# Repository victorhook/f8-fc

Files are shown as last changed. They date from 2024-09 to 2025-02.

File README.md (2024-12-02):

# f8 fc - Open source brushed x8 AIO

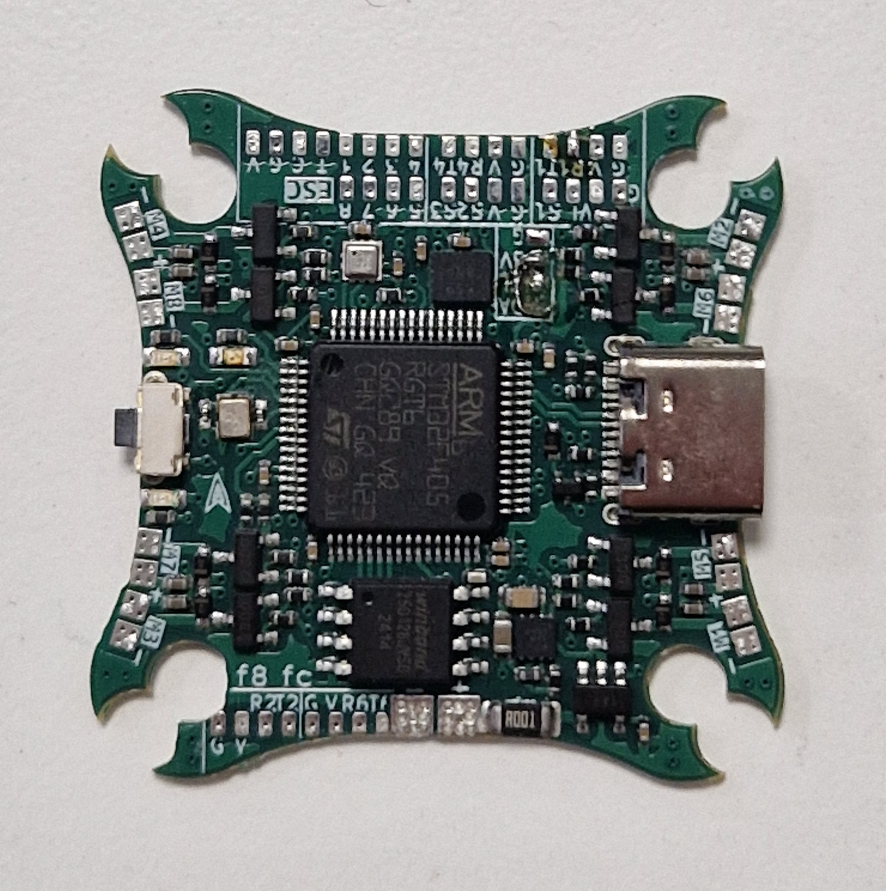
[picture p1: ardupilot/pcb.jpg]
PCB


[f8 fc](https://github.com/victorhook/f8-fc) is a fully open source AIO flight controller that is made primarily for small drones with brushed drones. It features:
- STM32F405 microcontroller with 1MB flash
- BMI270 imu
- BMP388 barometer
- Onboard 16MB external flash for data logging
- Status LEDs
- 1-4s input voltage
- 4 available UARTs
- **8** brushed motor drives with 6A mosfets
- Voltage & current sensing
- Runs ardupilot

## How to flash Ardupilot
1. Get ardupilot toolchain and put the `hwdef.dat` and `hwdef_bl.dat` in `ardupilot/libraries/AP_HAL_ChibiOS/hwdef/f8-fc/`
2. Build bootloader
```
./waf clean
./waf configure --board f8-fc --bootloader
./waf bootloader
```
3. Flash bootloader using something like STM32CubeProgrammer. Hold boot button when powering on the board to boot in DFU mode.
4. Build firmware and upload using the bootloader (have board plugged in to USB and ensure you get a new serial port)
```
./waf configure --board f8-fc
./waf copter --upload
```

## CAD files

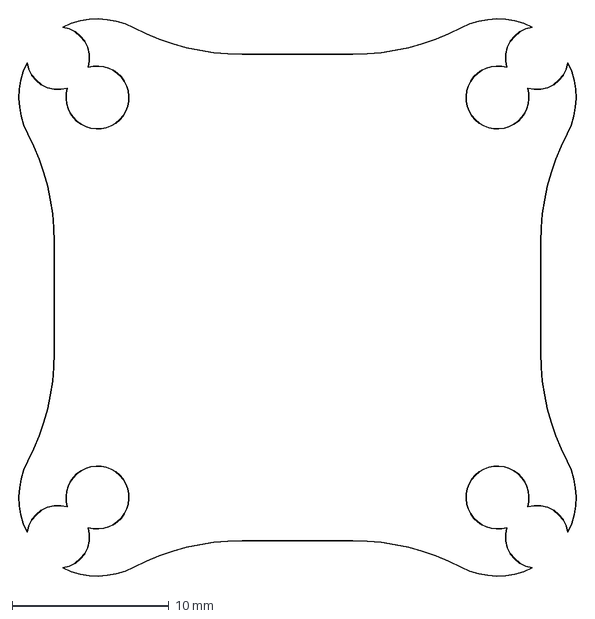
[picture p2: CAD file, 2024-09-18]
kicad/f8-fc-h7_rev-a/f8-fc_outline.dxf
35.9 x 35.9 mm

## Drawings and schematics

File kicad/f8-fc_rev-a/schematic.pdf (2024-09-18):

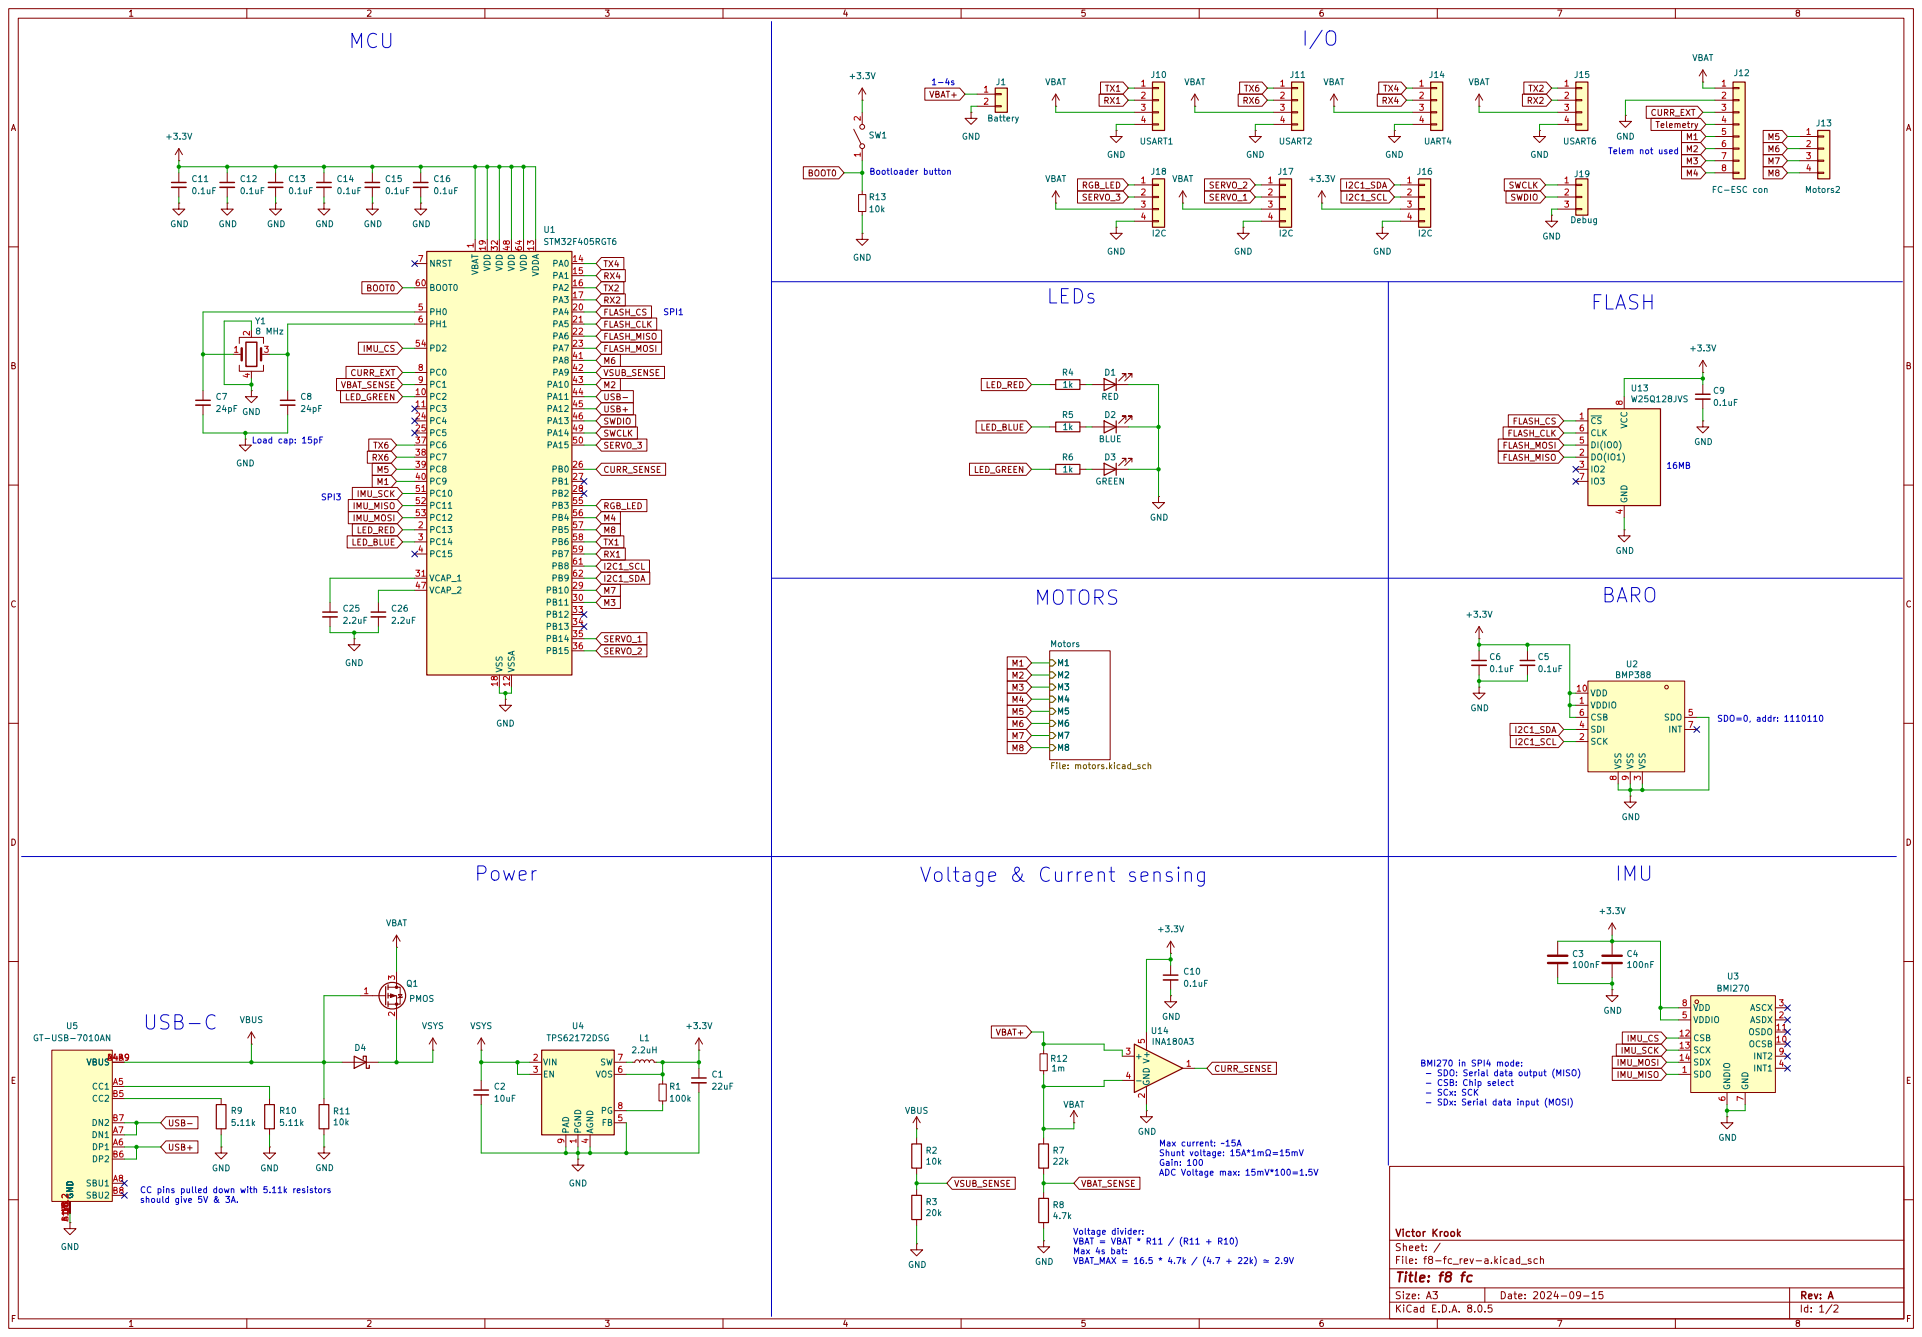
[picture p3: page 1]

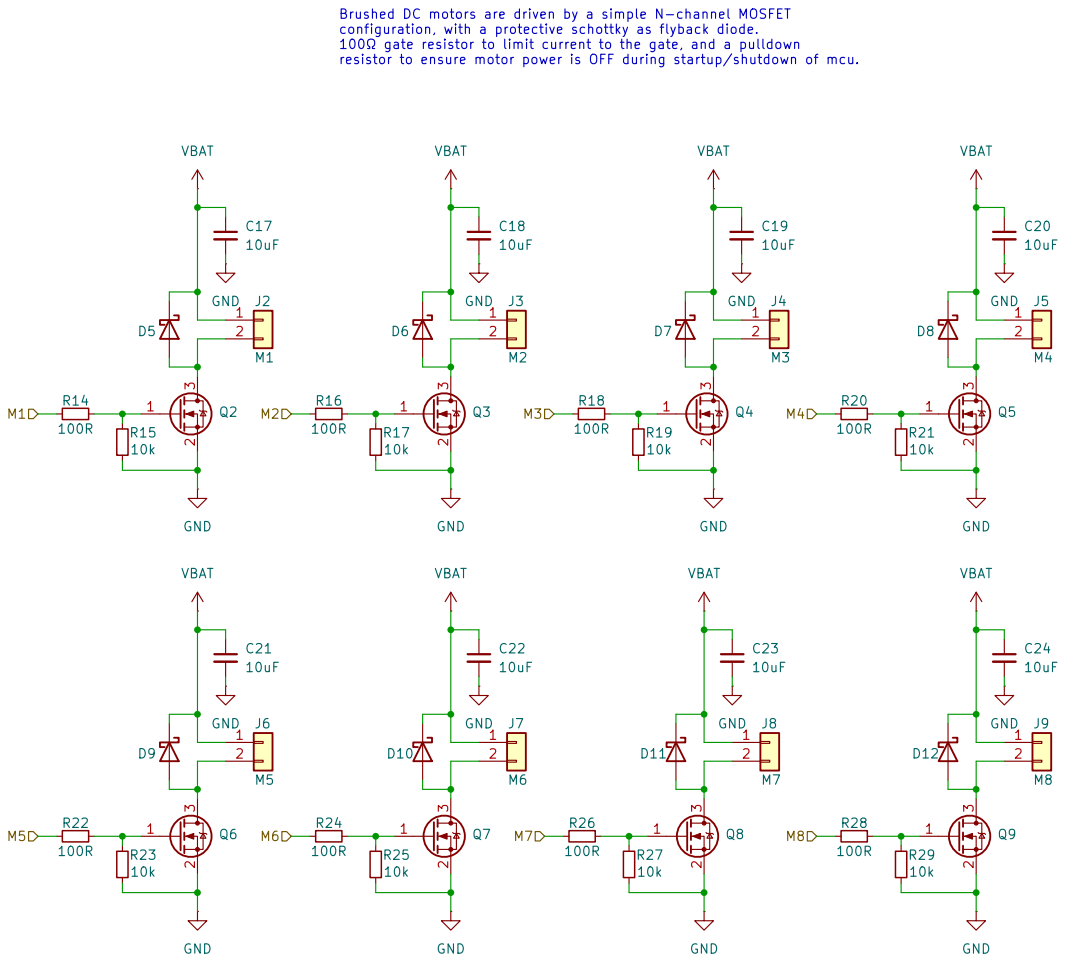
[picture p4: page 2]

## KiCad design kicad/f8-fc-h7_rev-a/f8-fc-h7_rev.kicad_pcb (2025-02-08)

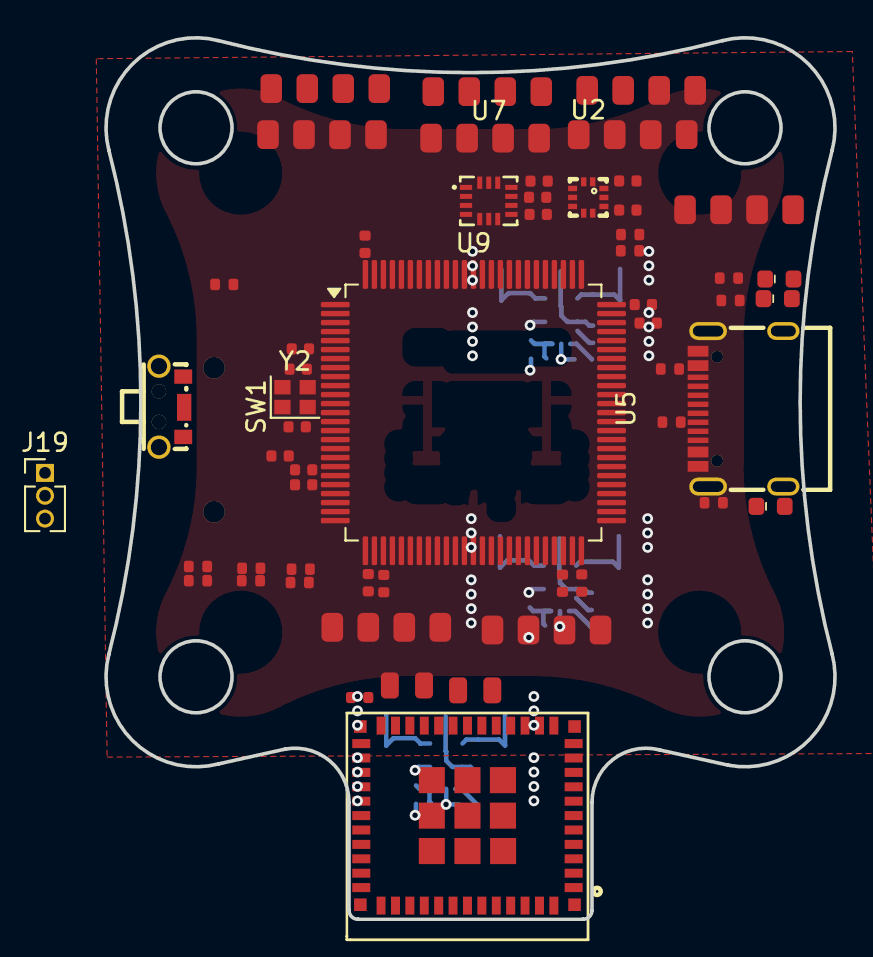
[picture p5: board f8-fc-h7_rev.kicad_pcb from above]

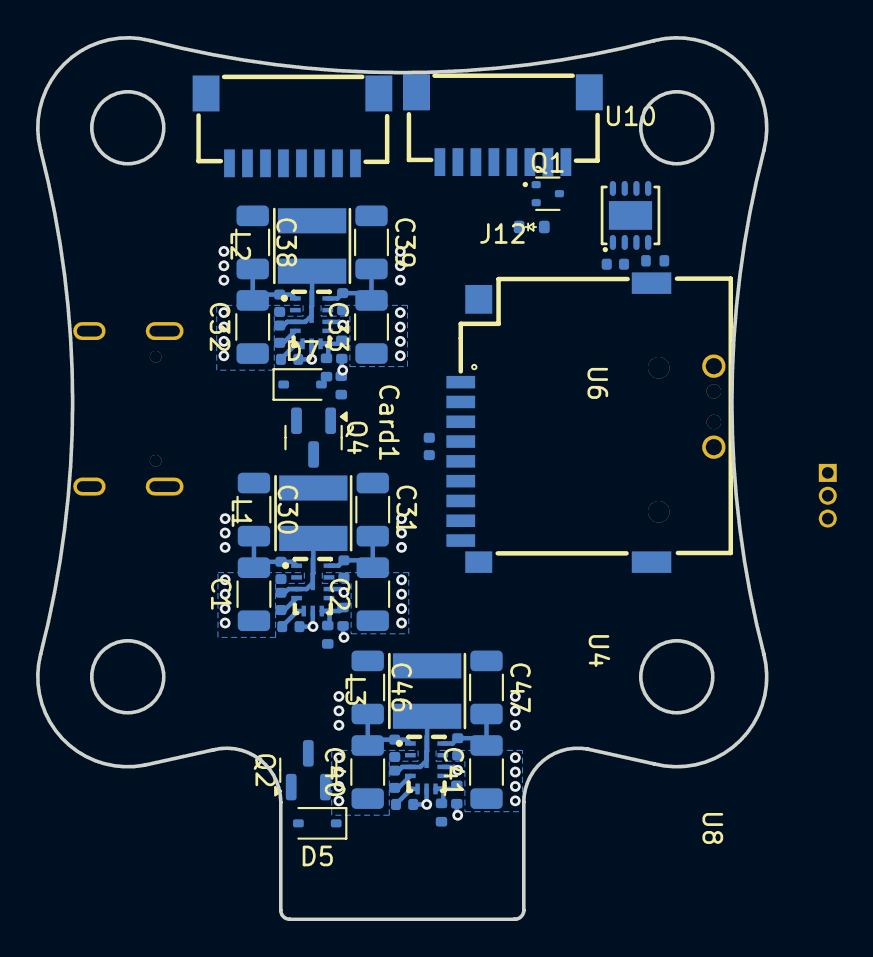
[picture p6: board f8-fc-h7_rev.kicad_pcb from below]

Board: 4 copper layers, 40.5 x 49.0 mm, 105 parts (50 on the bottom side), 46 nets.

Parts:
C1, C2, C32, C33, C40, C41: 10uF; C_1206_3216Metric
C3, C11: 10uF; C_0805_2012Metric_NoSilk
C4, C5, C6, C7, C9, C10, C17, C21, C22, C29, C37, C45, C48, C50, C52, C53, C54: 0.1uF; C_0402_1005Metric_NoSilk
C8: 4.7uF; C_0402_1005Metric_NoSilk
C18, C23: 15pF; C_0402_1005Metric_NoSilk
C19: 10nF; C_0402_1005Metric_NoSilk
C20, C49, C51: 2.2uF; C_0402_1005Metric_NoSilk
C24, C27, C34, C35, C42, C43: 220nF; C_0402_1005Metric_NoSilk
C28, C36, C44: 1uF; C_0402_1005Metric_NoSilk
C30, C31, C38, C39, C46, C47: 22uF; C_1206_3216Metric
Card1: TF PUSH; TF-SMD_TF-PUSH
D1: RED; LED_0603_1608Metric_NoSilk
D2: BLUE; LED_0603_1608Metric_NoSilk
D3: GREEN; LED_0603_1608Metric_NoSilk
D4: D_Schottky; D_SOD-523_NoSilk
D5, D7: D_Schottky; D_SOD-323
J1, J12: FC-ESC con; CONN-TH_SM08B-SRSS-TB-LF-SN
J10: USART1; Conn_4_Accesory_Bigger
J11: USART2; Conn_4_Accesory_Bigger
J14: UART4; Conn_4_Accesory_Bigger
J15: USART6; Conn_4_Accesory_Bigger
J16, J17, J18, J18#2, J18#3: I2C; Conn_4_Accesory_Bigger
J19: Debug; PinHeader_1x03_P1.27mm_Vertical
L1, L2, L3: 6.8uH; IND-SMD_L4.1-W4.1_ASFPIG4020
Q1: PMOS; SOT-523
Q2, Q4: WST4041; SOT-23
R1, R14, R16: 100k; R_0402_1005Metric_NoSilk
R2, R3, R11, R13, R20, R22, R23: 10k; R_0402_1005Metric_NoSilk
R4, R5, R6, R18: 1k; R_0402_1005Metric_NoSilk
R9, R10: 5.11k; R_0402_1005Metric_NoSilk
R12: 12.5K; R_0402_1005Metric_NoSilk
R15: 24.9k; R_0402_1005Metric_NoSilk
R17: 43.5k; R_0402_1005Metric_NoSilk
R24, R25: 2.2k; R_0402_1005Metric_NoSilk
R26: 120R; R_0402_1005Metric_NoSilk
SW1: SW_SPST; SW-SMD_TS-1086EV-16
U2: BMP388; SENSORM-SMD_BMP388
U3: ESP32-C3-MINI-1U-N4; WIFIM-SMD_61P-L13.2-W12.5-P0.80
U4, U6, U8: LMR33630AQRNXRQ1; VQFN-12_L3.0-W2.0-P0.65-BL_TI_RNX
U5: GT-USB-7010AN; USB-SMD_GT-USB-7010AN
U7: ICM-42688-P; LGA-14_L3.0-W2.5-P0.50-TL
U9: STM32H743VIT6; LQFP-100_14x14mm_P0.5mm
U10: SIT1050TK; TDFN-8_L3.0-W3.0-P0.65-BL-EP
Y2: 16 MHz; Crystal_SMD_2016-4Pin_2.0x1.6mm

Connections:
+3.3V: C3.1, C4.1, C5.1, C6.1, C8.1, C9.1, C10.1, C11.1, C17.1, C19.1, C20.1, C21.1, C22.1, C48.1, C50.1, C52.1, C53.1, C54.1, Card1.4 (VDD), J16.3, SW1.2 (B), U2.1 (VDDIO), U2.6 (CSB), U2.10 (VDD), U3.3 (3V3), U7.5 (VDDIO), U7.8 (VDD), U9.6 (VBAT), U9.11 (VDD), U9.20 (VREF+), U9.21 (VDDA), U9.27 (VDD), U9.50 (VDD), U9.75 (VDD), U9.100 (VDD), U10.5 (Vref)
+3V3: C46.1, C47.1, L3.2, R16.1, R24.1, R25.1
+4V5: C7.1, D7.1 (K), Q4.2 (S), U10.3 (VCC)
+5V: C30.1, C31.1, L1.2, Q4.3 (D), R1.1
+9V: C38.1, C39.1, L2.2, R14.1
BOOT0: R13.1, SW1.1 (A), U9.94 (BOOT0)
CANH: R26.1, U10.7 (CANH)
CANL: R26.2, U10.6 (CANL)
CURR_EXT: J1.3, J12.3
CURR_SENSE: R22.2, R23.1
GND: C1.2, C2.2, C3.2, C4.2, C5.2, C6.2, C7.2, C8.2, C9.2, C10.2, C11.2, C17.2, C18.2, C19.2, C20.2, C21.2, C22.2, C23.2, C24.2, C27.2, C28.1, C30.2, C31.2, C32.2, C33.2, C34.2, C35.2, C36.1, C38.2, C39.2, C40.2, C41.2, C42.2, C43.2, C44.1, C46.2, C47.2, C48.2, C49.2, C50.2, C51.2, C52.2, C53.2, C54.2, Card1.6 (VSS), D1.1 (K), D2.1 (K), D3.1 (K), J1.2, J10.4, J11.4, J12.2, J14.4, J15.4, J16.4, J17.4, J18.4, J18#2.4, J18#3.4, J19.3, R3.2, R9.2, R10.2, R12.2, R13.2, R15.2, R17.2, R18.2, R20.2, R23.2, U2.3 (VSS), U2.5 (SDO), U2.8 (VSS), U2.9 (VSS), U3.1 (GND), U3.2 (GND), U3.11 (GND), U3.14 (GND), U3.36 (GND), U3.37 (GND), U3.38 (GND), U3.39 (GND), U3.40 (GND), U3.41 (GND), U3.42 (GND), U3.43 (GND), U3.44 (GND), U3.45 (GND), U3.46 (GND), U3.47 (GND), U3.48 (GND), U3.49 (GND), U3.50 (GND), U3.51 (GND), U3.52 (GND), U3.53 (GND), U3.54 (GND), U3.55 (GND), U3.56 (GND), U3.57 (GND), U3.58 (GND), U3.59 (GND), U3.60 (GND), U3.61 (GND), U4.1 (PGND), U4.6 (AGND), U4.11 (PGND), U5.13 (GND), U5.14 (GND), U5.15 (GND), U5.16 (GND), U5.A1B12 (GND), U5.B1A12 (GND), U6.1 (PGND), U6.6 (AGND), U6.11 (PGND), U7.6 (GND), U8.1 (PGND), U8.6 (AGND), U8.11 (PGND), U9.10 (VSS), U9.19 (VSSA), U9.26 (VSS), U9.49 (VSS), U9.74 (VSS), U9.99 (VSS), U10.2 (GND), U10.8 (S), U10.9 (EP), Y2.2, Y2.4
I2C1_SCL: J16.2, R25.2, U2.2 (SCK)
I2C1_SDA: J16.1, R24.2, U2.4 (SDI)
unnamed: C49.1, U9.48 (VCAP)
unnamed: C51.1, U9.73 (VCAP)
unnamed: D1.2 (A), R4.1
unnamed: D2.2 (A), R5.1
unnamed: D3.2 (A), R6.1
unnamed: C29.1, U4.4 (BOOT)
unnamed: R1.2, R12.1, U4.7 (FB)
unnamed: C29.2, L1.1, U4.3 (NC), U4.12 (SW)
unnamed: C28.2, U4.5 (VCC)
unnamed: R10.1, U5.A5 (CC1)
unnamed: R9.1, U5.B5 (CC2)
unnamed: C37.1, U6.4 (BOOT)
unnamed: R14.2, R15.1, U6.7 (FB)
unnamed: C37.2, L2.1, U6.3 (NC), U6.12 (SW)
unnamed: C36.2, U6.5 (VCC)
unnamed: C45.1, U8.4 (BOOT)
unnamed: R16.2, R17.1, U8.7 (FB)
unnamed: C45.2, L3.1, U8.3 (NC), U8.12 (SW)
unnamed: C44.2, U8.5 (VCC)
unnamed: C18.1, U9.12 (PH0), Y2.1
unnamed: C23.1, U9.13 (PH1), Y2.3
RGB_LED: J18.1, J18#2.1, J18#3.1
SERVO_3: J18.2, J18#2.2, J18#3.2
SWCLK: J19.1, U9.76 (PA14)
SWDIO: J19.2, U9.72 (PA13)
Telemetry: J1.4, J12.4
USB+: U5.A6 (DP1), U5.B6 (DP2), U9.71 (PA12)
USB-: U5.A7 (DN1), U5.B7 (DN2), U9.70 (PA11)
VBAT: C1.1, C2.1, C24.1, C27.1, C32.1, C33.1, C34.1, C35.1, J1.1, J10.3, J11.3, J12.1, J14.3, J15.3, J17.3, J18.3, J18#2.3, J18#3.3, Q1.3 (D), R11.1, U4.2 (VIN), U4.9 (EN), U4.10 (VIN), U6.2 (VIN), U6.9 (EN), U6.10 (VIN)
VBAT_SENSE: R11.2, R18.1
VBUS: D4.2 (A), D5.2 (A), D7.2 (A), Q1.1 (G), Q4.1 (G), R2.1, R20.1, U5.A4B9 (VBUS), U5.B4A9 (VBUS)
VSUB_SENSE: R2.2, R3.1, U9.68 (PA9)
VSYS: C40.1, C41.1, C42.1, C43.1, D4.1 (K), D5.1 (K), Q1.2 (S), U8.2 (VIN), U8.9 (EN), U8.10 (VIN)

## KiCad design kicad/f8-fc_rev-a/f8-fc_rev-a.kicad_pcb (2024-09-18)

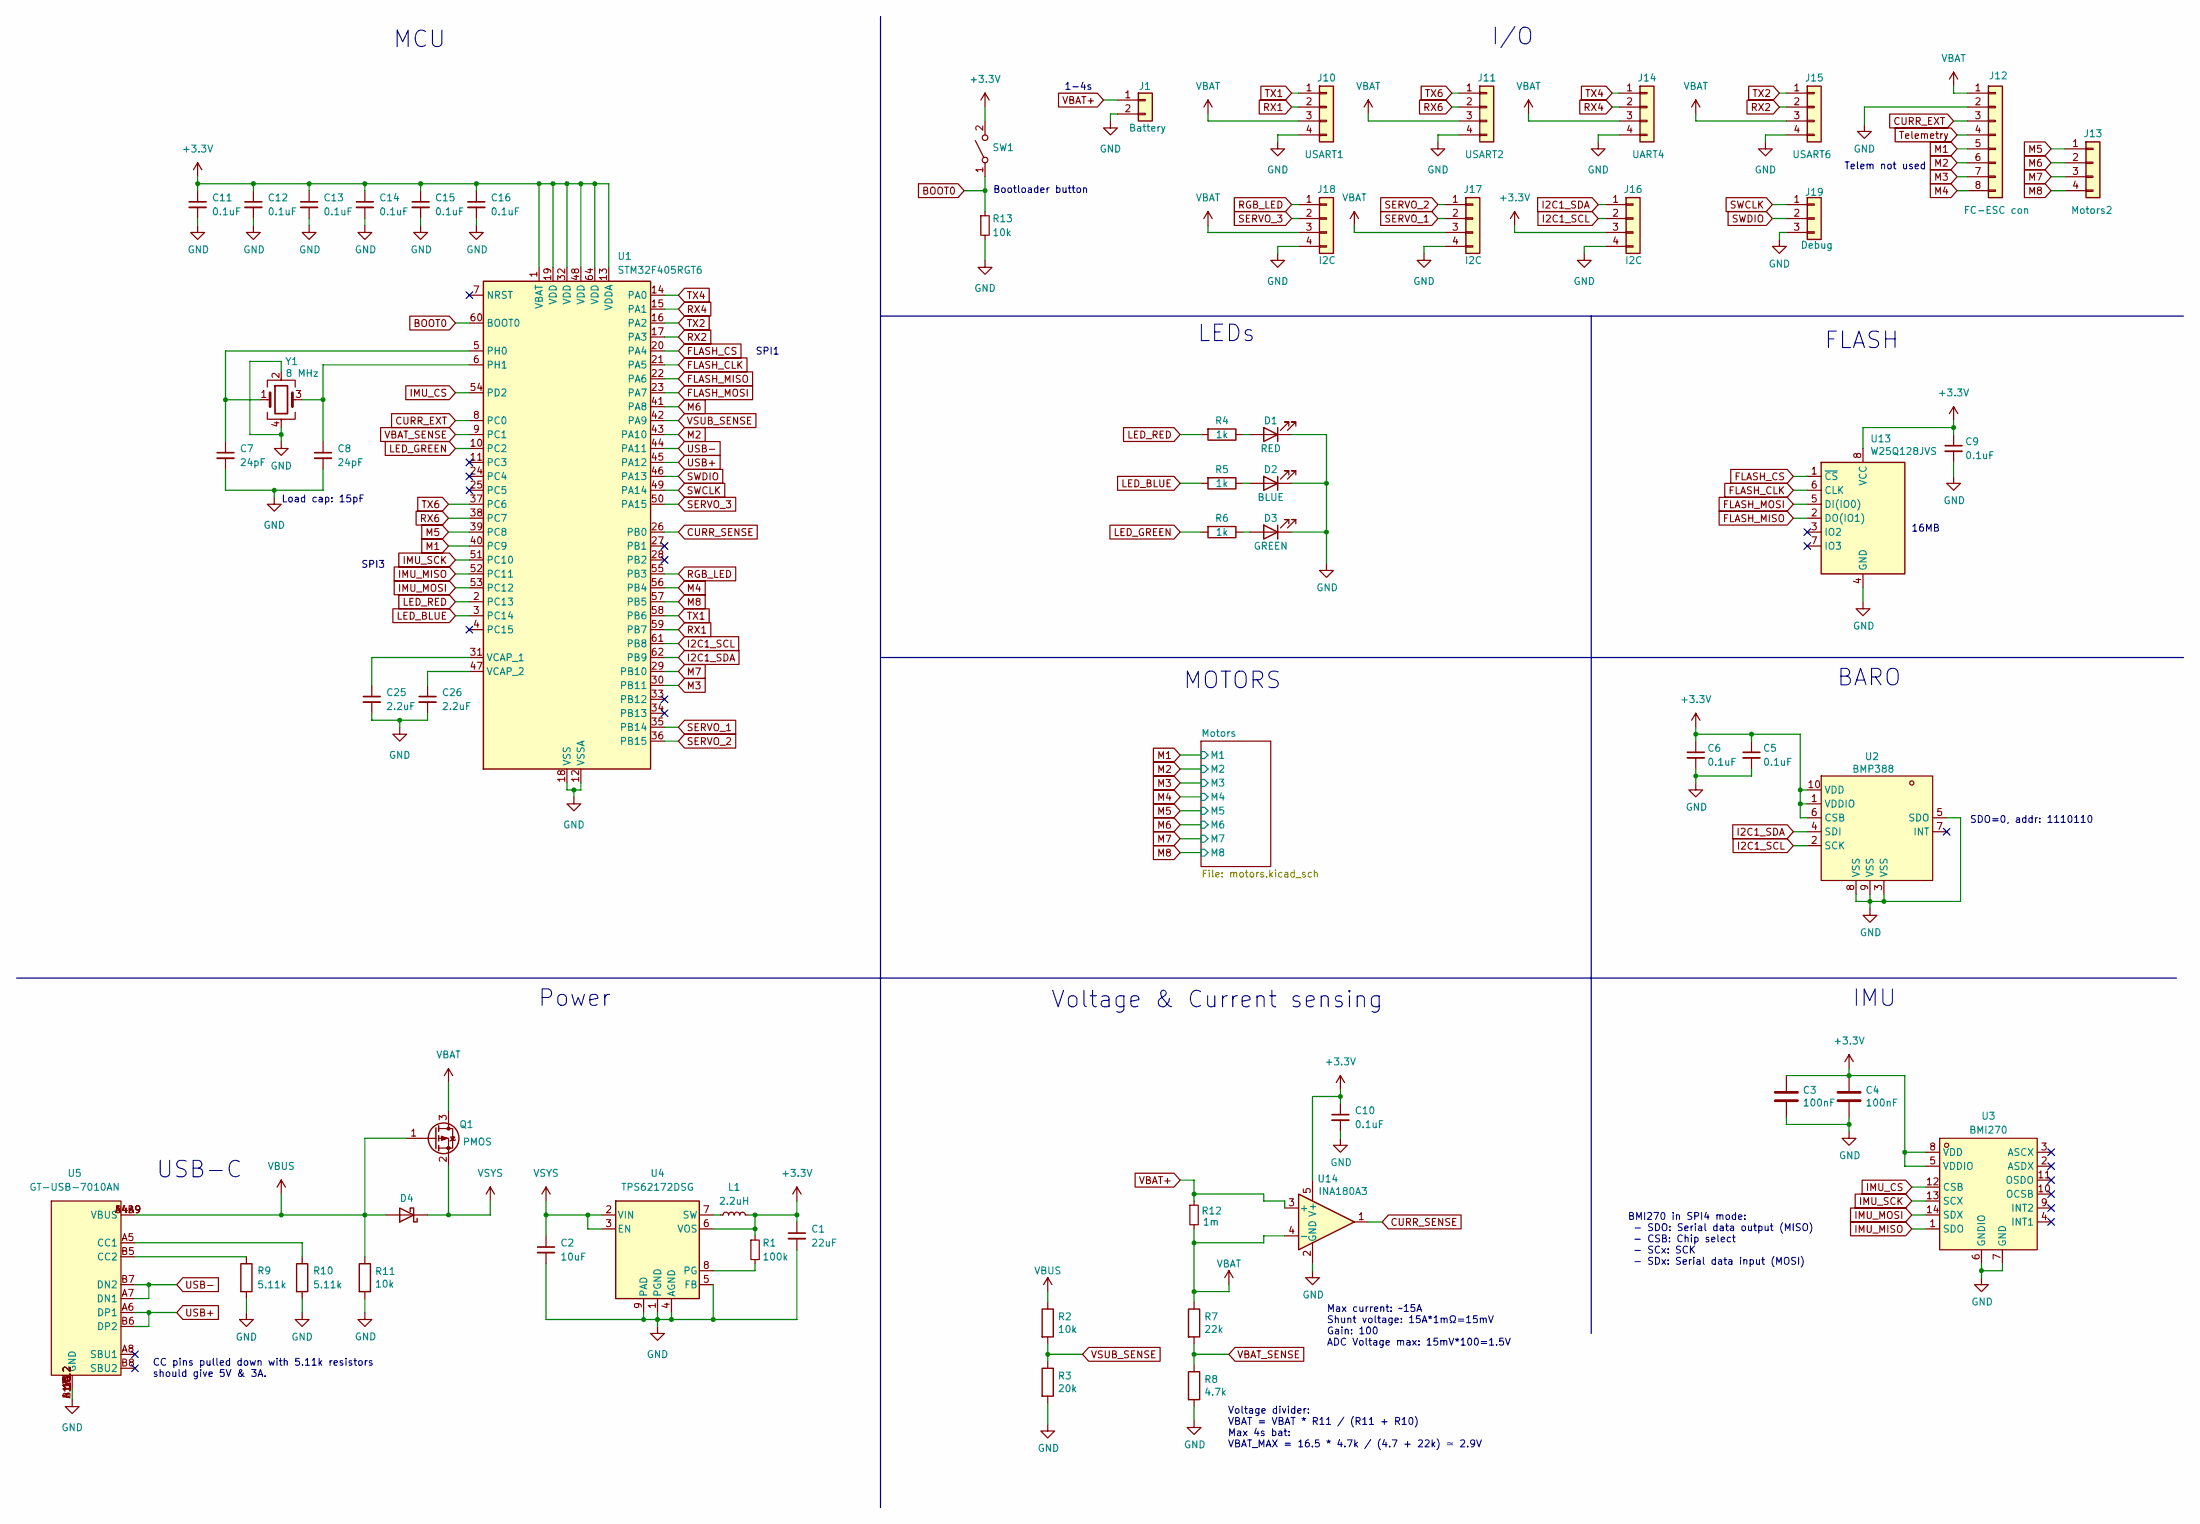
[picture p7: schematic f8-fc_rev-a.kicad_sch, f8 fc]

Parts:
C1: 22uF; C_0603_1608Metric_NoSilk
C2: 10uF; C_0603_1608Metric_NoSilk
C3, C4: 100nF; C_0402_1005Metric_NoSilk
C5, C6, C9, C10, C11, C12, C13, C14, C15, C16: 0.1uF; C_0402_1005Metric_NoSilk
C7, C8: 24pF; C_0402_1005Metric_NoSilk
C25, C26: 2.2uF; C_0402_1005Metric_NoSilk
D1: RED; LED_0603_1608Metric_NoSilk
D2: BLUE; LED_0603_1608Metric_NoSilk
D3: GREEN; LED_0603_1608Metric_NoSilk
D4: D_Schottky; D_SOD-523_NoSilk; LCSC Part C455040
J1: Battery; Conn_2_Bat
J10: USART1; Conn_4_Accesory
J11: USART2; Conn_4_Accesory
J12: FC-ESC con; Conn_8_Accesory
J13: Motors2; Conn_4_Accesory
J14: UART4; Conn_4_Accesory
J15: USART6; Conn_4_Accesory
J16, J17, J18: I2C; Conn_4_Accesory
J19: Debug; PinHeader_1x03_P1.27mm_Vertical
L1: 2.2uH; L_0402_1005Metric
Q1: PMOS; SOT-523; LCSC Part C5334586
R1: 100k; R_0402_1005Metric_NoSilk
R2, R11, R13: 10k; R_0402_1005Metric_NoSilk
R3: 20k; R_0402_1005Metric_NoSilk
R4, R5, R6: 1k; R_0402_1005Metric_NoSilk
R7: 22k; R_0402_1005Metric_NoSilk
R8: 4.7k; R_0402_1005Metric_NoSilk
R9, R10: 5.11k; R_0402_1005Metric_NoSilk
R12: 1m; R_1206_3216Metric; LCSC Part C7419993
SW1: SW_SPST; SW-SMD_TS-1086EV-16
U1: STM32F405RGT6; LQFP-64_10x10mm_P0.5mm
U2: BMP388; SENSORM-SMD_BMP388; LCSC Part C779278
U3: BMI270; LGA-14_L3.0-W2.5-P0.50-BR; LCSC Part C2836813
U4: TPS62172DSG; WSON-8-1EP_2x2mm_P0.5mm_EP0.9x1.6mm_ThermalVias
U5: GT-USB-7010AN; USB-SMD_GT-USB-7010AN; LCSC Part C963370
U13: W25Q128JVS; SOIC-8_5.23x5.23mm_P1.27mm; LCSC Part C97521
U14: INA180A3; SOT-23-5; LCSC Part C122882
Y1: 8 MHz; Crystal_SMD_2016-4Pin_2.0x1.6mm; LCSC Part C2831375

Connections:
+3.3V: C1.1, C3.1, C4.1, C5.1, C6.1, C9.1, C10.1, C11.1, C12.1, C13.1, C14.1, C15.1, C16.1, J16.3, L1.2, R1.1, SW1.2 (B), U1.1 (VBAT), U1.13 (VDDA), U1.19 (VDD), U1.32 (VDD), U1.48 (VDD), U1.64 (VDD), U2.1 (VDDIO), U2.6 (CSB), U2.10 (VDD), U3.5 (VDDIO), U3.8 (VDD), U4.6 (VOS), U13.8 (VCC), U14.5 (V+)
BOOT0: R13.1, SW1.1 (A), U1.60 (BOOT0)
CURR_EXT: J12.3, U1.8 (PC0)
CURR_SENSE: U1.26 (PB0), U14.1
FLASH_CLK: U1.21 (PA5), U13.6 (CLK)
FLASH_CS: U1.20 (PA4), U13.1 (~CS)
FLASH_MISO: U1.22 (PA6), U13.2 (DO(IO1))
FLASH_MOSI: U1.23 (PA7), U13.5 (DI(IO0))
GND: C1.2, C2.2, C3.2, C4.2, C5.2, C6.2, C7.2, C8.2, C9.2, C10.2, C11.2, C12.2, C13.2, C14.2, C15.2, C16.2, C25.2, C26.2, D1.1 (K), D2.1 (K), D3.1 (K), J1.2, J10.4, J11.4, J12.2, J14.4, J15.4, J16.4, J17.4, J18.4, J19.3, R3.2, R8.2, R9.2, R10.2, R11.2, R13.2, U1.12 (VSSA), U1.18 (VSS), U1.63 (VSS), U2.3 (VSS), U2.5 (SDO), U2.8 (VSS), U2.9 (VSS), U3.6 (GNDIO), U3.7 (GND), U4.1 (PGND), U4.4 (AGND), U4.5 (FB), U4.9 (PAD), U5.13 (GND), U5.14 (GND), U5.15 (GND), U5.16 (GND), U5.A1B12 (GND), U5.B1A12 (GND), U13.4 (GND), U14.2 (GND), Y1.2, Y1.4; also elsewhere on the board
I2C1_SCL: J16.2, U1.61 (PB8), U2.2 (SCK)
I2C1_SDA: J16.1, U1.62 (PB9), U2.4 (SDI)
IMU_CS: U1.54 (PD2), U3.12 (CSB)
IMU_MISO: U1.52 (PC11), U3.1 (SDO)
IMU_MOSI: U1.53 (PC12), U3.14 (SDX)
IMU_SCK: U1.51 (PC10), U3.13 (SCX)
LED_BLUE: R5.2, U1.3 (PC14)
LED_GREEN: R6.2, U1.10 (PC2)
LED_RED: R4.2, U1.2 (PC13)
M1: J12.5, U1.40 (PC9); also elsewhere on the board
M2: J12.6, U1.43 (PA10); also elsewhere on the board
M3: J12.7, U1.30 (PB11); also elsewhere on the board
M4: J12.8, U1.56 (PB4); also elsewhere on the board
M5: J13.1, U1.39 (PC8); also elsewhere on the board
M6: J13.2, U1.41 (PA8); also elsewhere on the board
M7: J13.3, U1.29 (PB10); also elsewhere on the board
M8: J13.4, U1.57 (PB5); also elsewhere on the board
unnamed: D1.2 (A), R4.1
unnamed: D2.2 (A), R5.1
unnamed: D3.2 (A), R6.1
unnamed: C7.1, U1.5 (PH0), Y1.1
unnamed: C8.1, U1.6 (PH1), Y1.3
unnamed: C25.1, U1.31 (VCAP_1)
unnamed: C26.1, U1.47 (VCAP_2)
unnamed: R1.2, U4.8 (PG)
unnamed: L1.1, U4.7 (SW)
unnamed: R10.1, U5.A5 (CC1)
unnamed: R9.1, U5.B5 (CC2)
RGB_LED: J18.1, U1.55 (PB3)
RX1: J10.2, U1.59 (PB7)
RX2: J15.2, U1.17 (PA3)
RX4: J14.2, U1.15 (PA1)
RX6: J11.2, U1.38 (PC7)
SERVO_1: J17.2, U1.35 (PB14)
SERVO_2: J17.1, U1.36 (PB15)
SERVO_3: J18.2, U1.50 (PA15)
SWCLK: J19.1, U1.49 (PA14)
SWDIO: J19.2, U1.46 (PA13)
TX1: J10.1, U1.58 (PB6)
TX2: J15.1, U1.16 (PA2)
TX4: J14.1, U1.14 (PA0)
TX6: J11.1, U1.37 (PC6)
Telemetry: J12.4
USB+: U1.45 (PA12), U5.A6 (DP1), U5.B6 (DP2)
USB-: U1.44 (PA11), U5.A7 (DN1), U5.B7 (DN2)
VBAT: J10.3, J11.3, J12.1, J14.3, J15.3, J17.3, J18.3, Q1.3 (D), R7.1, R12.2, U14.4 (-); also elsewhere on the board
VBAT+: J1.1, R12.1, U14.3 (+)
VBAT_SENSE: R7.2, R8.1, U1.9 (PC1)
VBUS: D4.2 (A), Q1.1 (G), R2.1, R11.1, U5.A4B9 (VBUS), U5.B4A9 (VBUS)
VSUB_SENSE: R2.2, R3.1, U1.42 (PA9)
VSYS: C2.1, D4.1 (K), Q1.2 (S), U4.2 (VIN), U4.3 (EN)

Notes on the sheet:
Max current: ~15A Shunt voltage: 15A*1mΩ=15mV Gain: 100 ADC Voltage max: 15mV*100=1.5V
MCU
SDO=0, addr: 1110110
BMI270 in SPI4 mode: - SDO: Serial data output (MISO) - CSB: Chip select - SCx: SCK - SDx: Serial data input (MOSI)
16MB
Telem not used
Voltage & Current sensing
LEDs
FLASH
IMU
I/O
CC pins pulled down with 5.11k resistors should give 5V & 3A.
Bootloader button
BARO
Load cap: 15pF
Voltage divider: VBAT = VBAT * R11 / (R11 + R10) Max 4s bat: VBAT_MAX = 16.5 * 4.7k / (4.7 + 22k) ≃ 2.9V
Power
SPI3
USB-C
SPI1
1-4s
MOTORS

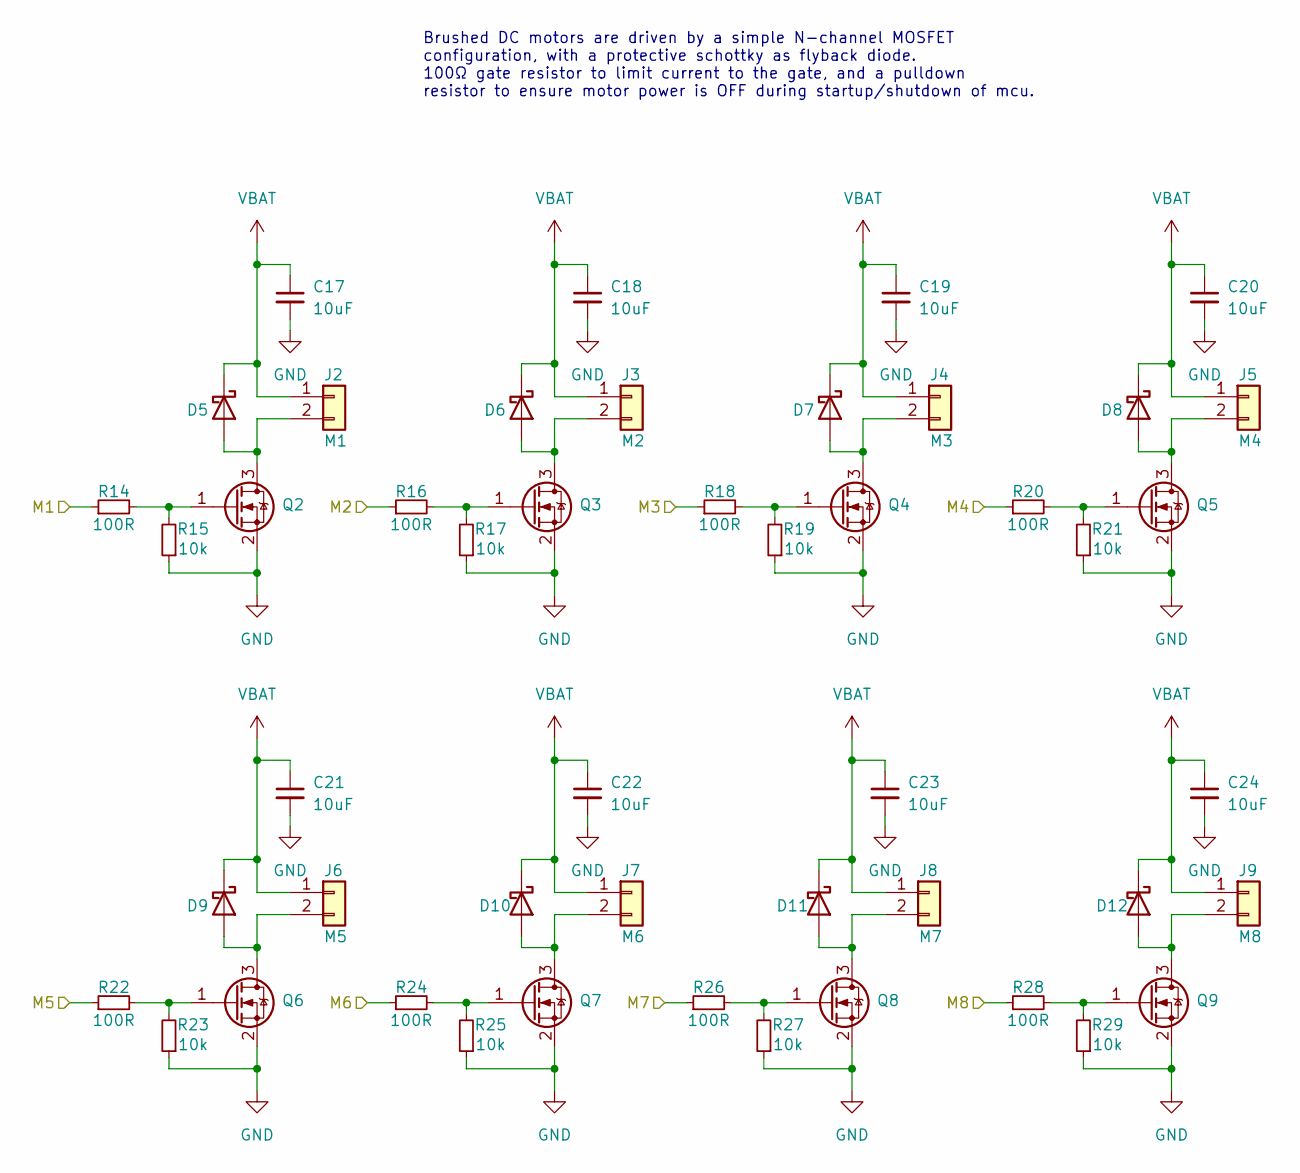
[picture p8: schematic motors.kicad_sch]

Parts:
C17, C18, C19, C20, C21, C22, C23, C24: 10uF; C_0402_1005Metric_NoSilk
D5, D6, D7, D8, D9, D10, D11, D12: D_Schottky; D_SOD-523_NoSilk; LCSC Part C455040
J2: M1; Conn_2_Motors
J3: M2; Conn_2_Motors
J4: M3; Conn_2_Motors
J5: M4; Conn_2_Motors
J6: M5; Conn_2_Motors
J7: M6; Conn_2_Motors
J8: M7; Conn_2_Motors
J9: M8; Conn_2_Motors
Q2, Q3, Q4, Q5, Q6, Q7, Q8, Q9: 2300A; SOT-23_NoSilk; LCSC Part C7437077
R14, R16, R18, R20, R22, R24, R26, R28: 100R; R_0402_1005Metric_NoSilk
R15, R17, R19, R21, R23, R25, R27, R29: 10k; R_0402_1005Metric_NoSilk

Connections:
GND: C17.2, C18.2, C19.2, C20.2, C21.2, C22.2, C23.2, C24.2, Q2.2 (S), Q3.2 (S), Q4.2 (S), Q5.2 (S), Q6.2 (S), Q7.2 (S), Q8.2 (S), Q9.2 (S), R15.1, R17.1, R19.1, R21.1, R23.1, R25.1, R27.1, R29.1; also elsewhere on the board
M1: R14.1; also elsewhere on the board
M2: R16.1; also elsewhere on the board
M3: R18.1; also elsewhere on the board
M4: R20.1; also elsewhere on the board
M5: R22.1; also elsewhere on the board
M6: R24.1; also elsewhere on the board
M7: R26.1; also elsewhere on the board
M8: R28.1; also elsewhere on the board
unnamed: D5.2 (A), J2.2, Q2.3 (D)
unnamed: D6.2 (A), J3.2, Q3.3 (D)
unnamed: D7.2 (A), J4.2, Q4.3 (D)
unnamed: D8.2 (A), J5.2, Q5.3 (D)
unnamed: D9.2 (A), J6.2, Q6.3 (D)
unnamed: D10.2 (A), J7.2, Q7.3 (D)
unnamed: D11.2 (A), J8.2, Q8.3 (D)
unnamed: D12.2 (A), J9.2, Q9.3 (D)
unnamed: Q2.1 (G), R14.2, R15.2
unnamed: Q3.1 (G), R16.2, R17.2
unnamed: Q4.1 (G), R18.2, R19.2
unnamed: Q5.1 (G), R20.2, R21.2
unnamed: Q6.1 (G), R22.2, R23.2
unnamed: Q7.1 (G), R24.2, R25.2
unnamed: Q8.1 (G), R26.2, R27.2
unnamed: Q9.1 (G), R28.2, R29.2
VBAT: C17.1, C18.1, C19.1, C20.1, C21.1, C22.1, C23.1, C24.1, D5.1 (K), D6.1 (K), D7.1 (K), D8.1 (K), D9.1 (K), D10.1 (K), D11.1 (K), D12.1 (K), J2.1, J3.1, J4.1, J5.1, J6.1, J7.1, J8.1, J9.1; also elsewhere on the board

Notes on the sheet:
Brushed DC motors are driven by a simple N-channel MOSFET configuration, with a protective schottky as flyback diode. 100Ω gate resistor to limit current to the gate, and a pulldown resistor to ensure motor power is OFF during startup/shutdown of mcu.

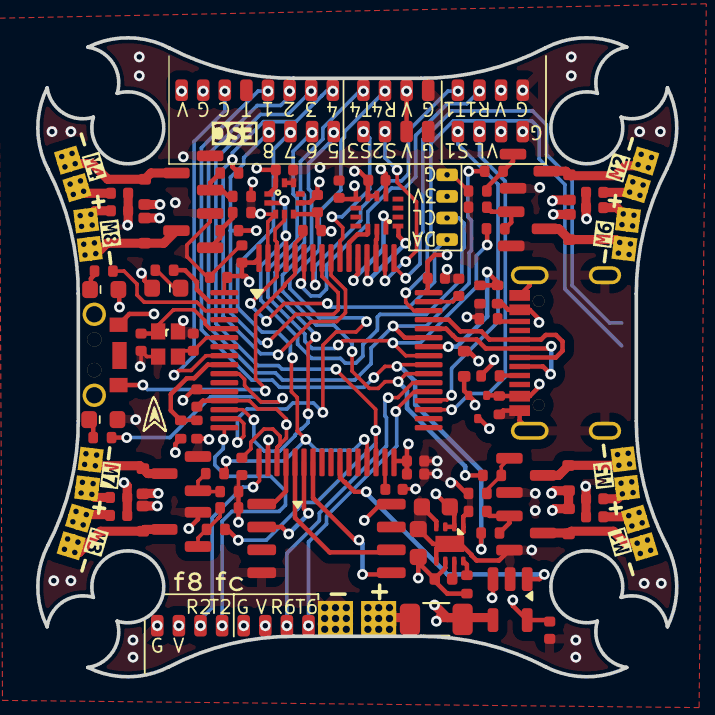
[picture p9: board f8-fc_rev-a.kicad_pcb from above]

Board: 4 copper layers, 35.5 x 35.5 mm, 114 parts (1 on the bottom side), 75 nets.

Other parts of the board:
kibuzzard-66DD79C8: G***; kibuzzard-66DD79C8
kibuzzard-66DD79DA: G***; kibuzzard-66DD79DA
kibuzzard-66DD778E: G***; kibuzzard-66DD778E
kibuzzard-66DD7786: G***; kibuzzard-66DD7786
kibuzzard-66E556E1: G***; kibuzzard-66E556E1
kibuzzard-66E556E7: G***; kibuzzard-66E556E7
kibuzzard-66E3374B: G***; kibuzzard-66E3374B
kibuzzard-66E5570F: G***; kibuzzard-66E5570F
kibuzzard-66E55715: G***; kibuzzard-66E55715

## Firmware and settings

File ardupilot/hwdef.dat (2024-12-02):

# hw definition file for processing by chibios_hwdef.py
# for f8 fc hardware.

# MCU class and specific type
# STM32F405RGT6
MCU STM32F4xx STM32F405xx

# board ID for firmware load
APJ_BOARD_ID 1299

# crystal frequency, setup to use external oscillator
OSCILLATOR_HZ 16000000

FLASH_SIZE_KB 1024

# bootloader takes first sector
FLASH_RESERVE_START_KB 64

define HAL_STORAGE_SIZE 16384
define STORAGE_FLASH_PAGE 1

STM32_ST_USE_TIMER 5

#optimize for space
env OPTIMIZE -Os

# These are the pins for SWD debugging with a STlinkv2 or black-magic probe.
PA13 JTMS-SWDIO SWD
PA14 JTCK-SWCLK SWD

# -- USB -- #
USB_STRING_MANUFACTURER "f8 fc"

# USB
PA11 OTG_FS_DM OTG1
PA12 OTG_FS_DP OTG1

# OTG USB VBUS (USB detect)
#PA9 VBUS INPUT

# -- SPI devices -- ##
SPIDEV bmi270    SPI3 DEVID1 IMU_CS    MODE3 10*MHZ 10*MHZ
SPIDEV dataflash SPI1 DEVID2 FLASH_CS  MODE3 32*MHZ 32*MHZ

# SPI1 for W25Q128JVS dataflash
PA5 SPI1_SCK SPI1
PA6 SPI1_MISO SPI1
PA7 SPI1_MOSI SPI1
PA4 FLASH_CS CS

# SPI3 for BMI270 IMU
PC10 SPI3_SCK SPI3
PC11 SPI3_MISO SPI3
PC12 SPI3_MOSI SPI3
PD2 IMU_CS CS

# -- SERIAL ports -- #
SERIAL_ORDER OTG1 USART1 USART2 UART4 USART6

# USART1
PB6 USART1_TX USART1
PB7 USART1_RX USART1

# USART2
PA2 USART2_TX USART2
PA3 USART2_RX USART2

# UART4
PA0 UART4_TX UART4 NODMA
PA1 UART4_RX UART4 NODMA

# USART6
PC6 USART6_TX USART6
PC7 USART6_RX USART6

# -- I2C ports -- #
I2C_ORDER I2C1

# I2C1
PB8 I2C1_SCL I2C1
PB9 I2C1_SDA I2C1

# -- ADC ports -- #
define HAL_BATT_MONITOR_DEFAULT 4

# Current
PB0 BATT_CURRENT_SENS ADC1 SCALE(1)
define HAL_BATT_CURR_PIN 8
define HAL_BATT_CURR_SCALE 70.8

# Voltage
PC1 BATT_VOLTAGE_SENS ADC1 SCALE(1)
define HAL_BATT_VOLT_PIN 11
define HAL_BATT_VOLT_SCALE 11.0

# Current (external)
PC0 BATT_CURRENT_SENS2 ADC1 SCALE(1)
define HAL_BATT2_CURR_PIN 10
define HAL_BATT2_CURR_SCALE 10

# Voltage (external, same pin as internal)
define HAL_BATT2_VOLT_PIN 11
define HAL_BATT2_VOLT_SCALE 11.0

# -- MOTORS -- #
PC9  TIM3_CH4  TIM3  PWM(1) GPIO(50) # M1
PA10 TIM1_CH3  TIM1  PWM(2) GPIO(51) # M2
PB11 TIM2_CH4  TIM2  PWM(3) GPIO(52) # M3
PB4  TIM3_CH1  TIM3  PWM(4) GPIO(53) # M4
PC8  TIM3_CH3  TIM3  PWM(5) GPIO(54) # M5
PA8  TIM1_CH1  TIM1  PWM(6) GPIO(55) # M6
PB10 TIM2_CH3  TIM2  PWM(7) GPIO(56) # M7
PB5  TIM3_CH2  TIM3  PWM(8) GPIO(57) # M8

# -- Servos -- #
PB15 TIM12_CH2 TIM12 PWM(9) GPIO(58) NODMA # S1
PA15 TIM2_CH1  TIM2  PWM(10) GPIO(59) NODMA # S2
PB14 TIM12_CH1 TIM12 PWM(11) GPIO(60) NODMA # S3

# -- RGB LED strip -- #
PB3  TIM2_CH2  TIM2  PWM(12) GPIO(61)

# -- LEDs -- #
PC14 LED0 OUTPUT LOW GPIO(90) # Blue
PC2  LED1 OUTPUT LOW GPIO(91) # Green
PC13 LED2 OUTPUT LOW GPIO(92) # Red
define AP_NOTIFY_GPIO_LED_1_ENABLED 1
define AP_NOTIFY_GPIO_LED_1_PIN 90
define HAL_GPIO_A_LED_PIN 90
define HAL_GPIO_B_LED_PIN 91
define HAL_GPIO_C_LED_PIN 92

# -- Dataflash setup -- #
define HAL_LOGGING_DATAFLASH_ENABLED 1

# -- OSD -- #
define HAL_OSD_TYPE_DEFAULT 1
ROMFS_WILDCARD libraries/AP_OSD/fonts/font*.bin

# -- BARO -- #
define AP_BARO_BACKEND_DEFAULT_ENABLED 0
define AP_BARO_BMP388_ENABLED 1
BARO BMP388 I2C:0:0x76

# -- IMU -- #
IMU BMI270 SPI:bmi270 ROTATION_YAW_180

# DMA_PRIORITY
DMA_NOSHARE SPI3 

# no built-in compass, but probe the i2c bus for all possible
# external compass types
define ALLOW_ARM_NO_COMPASS 1
define HAL_PROBE_EXTERNAL_I2C_COMPASSES 1
define HAL_I2C_INTERNAL_MASK 0
define HAL_COMPASS_AUTO_ROT_DEFAULT 2
define HAL_DEFAULT_INS_FAST_SAMPLE 1

# -- Defines to reduce fw size -- #
# disable emitting nice strings when activating RC channel aux functions:
define AP_RC_CHANNEL_AUX_FUNCTION_STRINGS_ENABLED 0

define HAL_HIGH_LATENCY2_ENABLED 0
define AP_GRIPPER_ENABLED 0
define HAL_SPRAYER_ENABLED 0
define HAL_GYROFFT_ENABLED 0
define AP_NOTIFY_NCP5623_ENABLED 0
define HAL_HOTT_TELEM_ENABLED 0

define AP_GPS_BACKEND_DEFAULT_ENABLED 0
define AP_GPS_UBLOX_ENABLED 0
define AP_GPS_DRONECAN_ENABLED 0
define HAL_ENABLE_DRONECAN_DRIVERS 0
undef HAL_MSP_GPS_ENABLED
define HAL_MSP_GPS_ENABLED 0
define HAL_MSP_SENSORS_ENABLED 0

define GPS_MOVING_BASELINE 0

define AP_LTM_TELEM_ENABLED 0

define NUM_SERVO_CHANNELS 11

define AP_WINCH_ENABLED 0

define AP_CAMERA_BACKEND_DEFAULT_ENABLED 0
define AP_CAMERA_RELAY_ENABLED AP_CAMERA_ENABLED
define AP_CAMERA_SERVO_ENABLED AP_CAMERA_ENABLED

define AP_CAN_SLCAN_ENABLED 0

define HAL_PICCOLO_CAN_ENABLE 0

define AP_BEACON_ENABLED 0

define AP_BATTERY_BACKEND_DEFAULT_ENABLED 0
define AP_BATTERY_ANALOG_ENABLED 1
define AP_BATTERY_ESC_ENABLED HAL_WITH_ESC_TELEM
define AP_BATTERY_WATT_MAX_ENABLED 0
define AP_BATTERY_UAVCAN_BATTERYINFO_ENABLED 0
define HAL_ENABLE_DRONECAN_DRIVERS 0
define AP_BATTERY_SUM_ENABLED 1
define AP_BATTERY_SYNTHETIC_CURRENT_ENABLED 0
define AP_BATTERY_SMBUS_ENABLED 0
define AP_BATTERY_SMBUS_GENERIC_ENABLED 0
define AP_BATTERY_SMBUS_ENABLED 0
define AP_BATTERY_SMBUS_NEODESIGN_ENABLED 0
define AP_BATTERY_SMBUS_ENABLED 0
define AP_BATTERY_SMBUS_SUI_ENABLED 0
define AP_BATTERY_SMBUS_ENABLED 0
define AP_BATTERY_SMBUS_MAXELL_ENABLED 0
define AP_BATTERY_SMBUS_ENABLED 0
define AP_BATTERY_SMBUS_ROTOYE_ENABLED 0
define AP_BATTERY_SMBUS_ENABLED 0

define AP_BARO_PROBE_EXTERNAL_I2C_BUSES 0

define HAL_BARO_WIND_COMP_ENABLED 0

define HAL_MOUNT_ENABLED 0

define HAL_GENERATOR_ENABLED 0

define HAL_NMEA_OUTPUT_ENABLED 0

define HAL_DISPLAY_ENABLED 0

define AP_INERTIALSENSOR_KILL_IMU_ENABLED 0

# shortened names in @SYS/taskinfo.txt
define AP_SCHEDULER_EXTENDED_TASKINFO_ENABLED 0

define AP_LANDINGGEAR_ENABLED 0
define APM_BUILD_COPTER_OR_HELI 0

# Plane-specific defines; these defines are only used in the Plane
#  directory, but are seen across the entire codebase:
define OFFBOARD_GUIDED 0
define QAUTOTUNE_ENABLED 0

# Copter-specific defines; these defines are only used in the Copter
#  directory, but are seen across the entire codebase:
define MODE_FLOWHOLD_ENABLED 0
define MODE_ZIGZAG_ENABLED 0
define AC_NAV_GUIDED 0
define AC_OAPATHPLANNER_ENABLED 0
define MODE_FOLLOW_ENABLED 0
define MODE_GUIDED_NOGPS_ENABLED 0
define MODE_SYSTEMID_ENABLED 0
define WEATHERVANE_ENABLED 0
define MODE_AUTOROTATE_ENABLED 0

# don't send RELAY_STATUS messages:
define AP_MAVLINK_MSG_RELAY_STATUS_ENABLED 0

#fewer airspeed sensors
define AP_AIRSPEED_BACKEND_DEFAULT_ENABLED 0
define AP_AIRSPEED_MS4525_ENABLED 0
define AP_AIRSPEED_ASP5033_ENABLED 0
define AP_AIRSPEED_ANALOG_ENABLED 0
define AP_AIRSPEED_MS5525_ENABLED 0
define AP_AIRSPEED_SDP3X_ENABLED 0
define AP_AIRSPEED_NMEA_ENABLED 0  # additional checks for vehicle type in .cpp
define AP_AIRSPEED_DRONECAN_ENABLED HAL_ENABLE_DRONECAN_DRIVERS

# don't need payload place mission items on these boards, it's very niche:
define AP_MISSION_NAV_PAYLOAD_PLACE_ENABLED 0
# don't need the payload place flight behaviour either:
define AC_PAYLOAD_PLACE_ENABLED 0


# -- Size reduction END -- #

define AP_OPTICALFLOW_ENABLED 1

#define HAL_OS_FATFS_IO 1

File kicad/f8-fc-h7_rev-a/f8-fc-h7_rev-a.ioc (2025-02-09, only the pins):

Mcu.UserName=STM32H743VITx
PA1.Signal=ETH_REF_CLK
PA11.Signal=USB_OTG_FS_DM
PA12.Signal=USB_OTG_FS_DP
PA2.Signal=ETH_MDIO
PA3.Signal=USART2_RX
PA7.Signal=ETH_CRS_DV
PA8.Signal=I2C3_SCL
PA9.Signal=USB_OTG_FS_VBUS
PB10.Signal=USART3_TX
PB11.Signal=ETH_TX_EN
PB12.Signal=ETH_TXD0
PB13.Signal=ETH_TXD1
PB14.Signal=USART1_TX
PB15.Signal=USART1_RX
PB5.Signal=GPIO_Output
PB6.Signal=S_TIM4_CH1
PB7.Signal=S_TIM4_CH2
PB8.Signal=S_TIM4_CH3
PB9.Signal=S_TIM4_CH4
PC1.Signal=ETH_MDC
PC10.Signal=SDMMC1_D2
PC11.Signal=SDMMC1_D3
PC12.Signal=SDMMC1_CK
PC4.Signal=ETH_RXD0
PC5.Signal=ETH_RXD1
PC6.Signal=USART6_TX
PC7.Signal=USART6_RX
PC8.Signal=SDMMC1_D0
PC9.Signal=I2C3_SDA
PD0.Signal=FDCAN1_RX
PD1.Signal=FDCAN1_TX
PD2.Signal=SDMMC1_CMD
PD6.Signal=GPIO_Input
PD7.Signal=SPI1_MOSI
PE0.Signal=UART8_RX
PE1.Signal=UART8_TX
PE11.Signal=S_TIM1_CH2
PE13.Signal=S_TIM1_CH3
PE14.Signal=S_TIM1_CH4
PE5.Signal=S_TIM15_CH1
PE6.Signal=S_TIM15_CH2
PE7.Signal=UART7_RX
PE8.Signal=UART7_TX
PE9.Signal=S_TIM1_CH1

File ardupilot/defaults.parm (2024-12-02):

# LED strip on PWM 12
SERVO13_FUNCTION 120
NTF_LED_TYPES 257
NTF_LED_LEN 1

# Brushed motors by default (onboard motor drivers)
MOT_PWM_TYPE 3

BATT_ARM_VOLT 3.6

BATT_LOW_VOLT 3.5
BATT_FS_LOW_ACT 0 # Do nothing

BATT_CRT_VOLT 3.45
BATT_FS_CRT_ACT 1 # Land

# Frame
FRAME_TYPE  12 # BetaFlightX
FRAME_CLASS 4  # OctaQuad

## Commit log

2024-09-12 More progress on pcb!
    [fc-brushed-aio-rev-a.kicad_pcb, fc-brushed-aio-rev-a.kicad_sch]
2024-09-14 Majority of routing complete. Schematic too.
    [fc-brushed-aio-rev-a.kicad_pcb, fc-brushed-aio-rev-a.kicad_sch]
2024-09-14 Got `hwdet.dat` file mostly complete. Can compile everything now
    [defaults.parm, fc-brushed-aio-rev-a.kicad_pcb, fc-brushed-aio-rev-a.kicad_sch]
2024-09-15 Almost done with pcb! Need final checks and some silkscreen design stuff
    [fc-brushed-aio-rev-a.kicad_pcb, fc-brushed-aio-rev-a.kicad_sch, motors.kicad_sch]
2024-09-15 Renamed project to "f8 fc"
    [f8-fc_rev-a.kicad_pcb, f8-fc_rev-a.kicad_sch, motors.kicad_sch]
2024-09-15 Added some silkscreen
    [f8-fc_rev-a.kicad_pcb]
2024-09-15 Clenaup: Almost ready for order
    Need to get the 30.5x30.5 holes into the outline as well, otherwise all looks good
    [f8-fc_rev-a.kicad_pcb, f8-fc_rev-a.kicad_sch, motors.kicad_sch]
2024-09-16 Updated some AP hwdef param stuff Was able to build fw with lua scripting enabled! Under 1MB!
    [defaults.parm]
2024-09-18 rev. A is ready to order!
    [f8-fc_outline.dxf, f8-fc_rev-a.kicad_pcb, f8-fc_rev-a.kicad_sch]
2024-09-18 Updated cap to 0603 (C2) and driver caps from 10uf to 1uf. This is because these needs to tolerate higher voltages than 10V and that isn't available at 0402 10uF..
    [f8-fc_rev-a.kicad_pcb, f8-fc_rev-a.kicad_sch]
2024-12-02 Added updated ardupilot parameter files
    [defaults.parm]
2025-02-05 Started on new board with h743 mcu
    [f8-fc-h7_rev-a.kicad_pcb, f8-fc-h7_rev.kicad_pcb, f8-fc-h7_rev.kicad_sch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]
2025-02-08 Initial ethernet PHY support
    Realized however that the IC chosen (DP83848TSQ/NOPB) which
    pixhawk uses in their example in Bus standard 6, isn't supported by Ardupilot.
    So should probably change IC
    [ethernet.kicad_sch, f8-fc-h7_rev.kicad_sch, power.kicad_sch]
2025-02-09 Swapped to LAN8742 Ethernet PHY
    This was is supported by AP so seems more safe
    to use this.
    Also seems a bit simpler in wiring as it has a few less pins.
    A downside is that I cannot find a proper application
    schematic example online..
    [ethernet.kicad_sch, f8-fc-h7_rev.kicad_pcb, f8-fc-h7_rev.kicad_sch]
